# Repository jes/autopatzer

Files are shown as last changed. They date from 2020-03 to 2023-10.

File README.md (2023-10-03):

# autopatzer

An automatic chess board, supporting online play with people all over the world via the [Lichess Boards API](https://lichess.org/blog/XlRW5REAAB8AUJJ-/welcome-lichess-boards).

This repo contains FreeCAD files for the mechanical design, KiCad files for PCB design, Arduino code to run on
the microcontroller, Perl code for the library/program that interfaces with the controller, and JavaScript code for the
user interface and Lichess interface.

You can [watch a video of the board](https://www.youtube.com/watch?v=8ScFtkWvHW8) if you want.

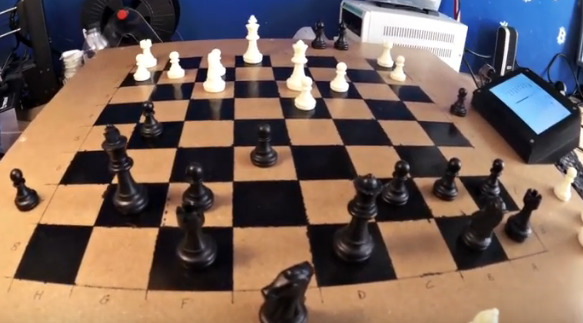
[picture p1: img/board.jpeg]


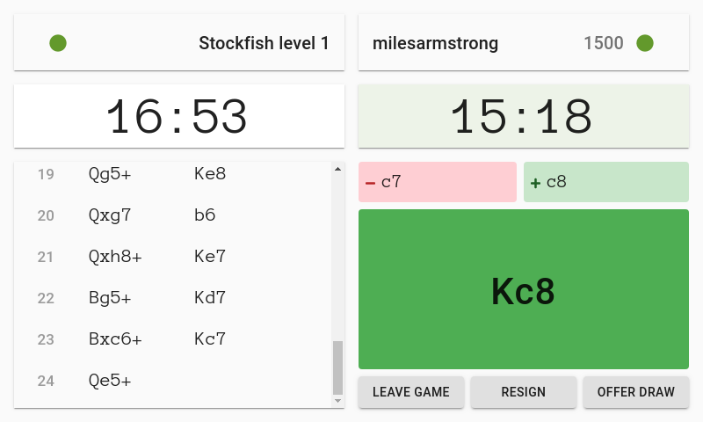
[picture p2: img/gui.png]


## Build one yourself

I thoroughly encourage you to build an Autopatzer board. You'll need:

 - 3d printer
 - soldering skills
 - general DIY skills
 - and it would probably help to have prior experience with Arduino and Raspberry Pi

There aren't currently a decent set of instructions, so if you want to build one let's try and write some
instructions as you go so that it might be easier for whoever comes next!

There are some notes about how you might want to change the design in my blog post: https://incoherency.co.uk/blog/stories/autopatzer.html

## Architecture

There is a NEMA17 stepper motor for each of the X and Y axis, from an old 3d printer. The stepper motors are controlled by A4988 stepper
motor drivers, which are controlled using the step/direction pins, driven by the AccelStepper Arduino library. The electromagnet is switched
on and off with a MOSFET. The pieces are detected with an analogue hall effect sensor under each square. These 64 analogue signals are reduced
to 8 signals with 8x CD4051 8-to-1 analogue multiplexers. All of the code for this runs on a Teensy 3.2 microcontroller, and the rest is
adequately explained by this diagram:

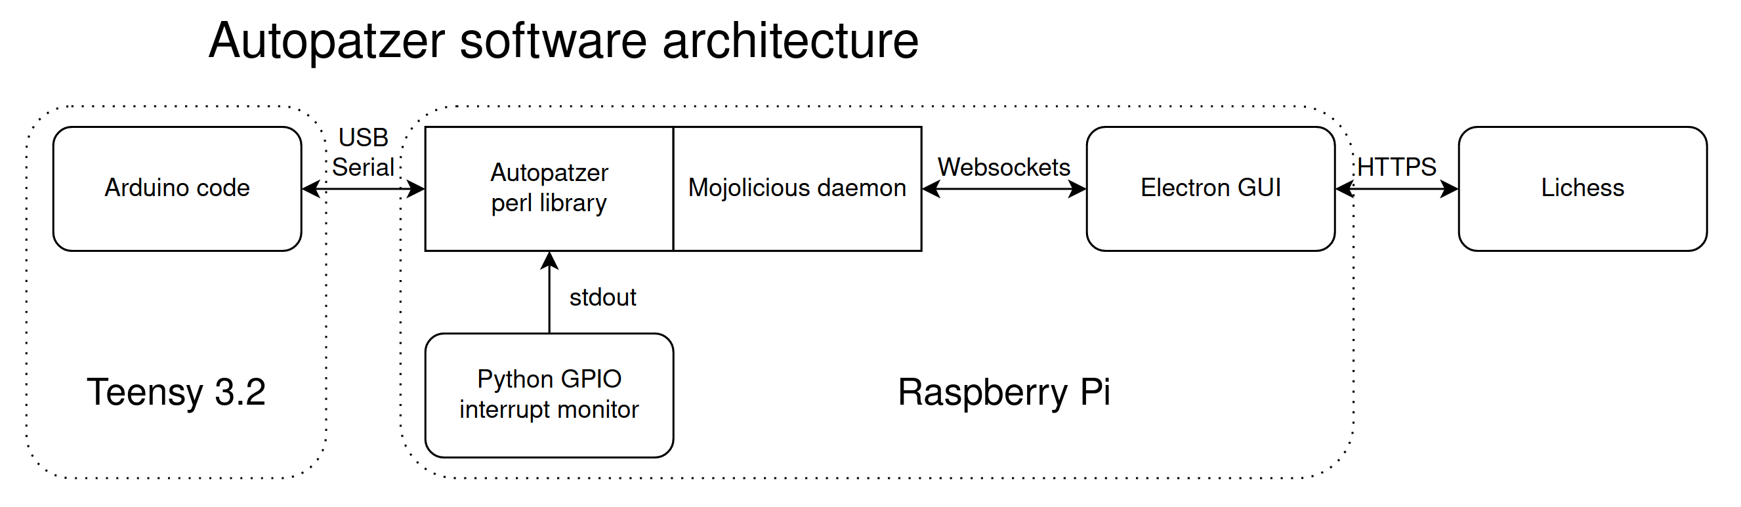
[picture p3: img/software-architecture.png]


## Contact

The Electron app providing the user interface is by Miles Armstrong: miles@milesarmstrong.co.uk

The rest is by James Stanley: james@incoherency.co.uk

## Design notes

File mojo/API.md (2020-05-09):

# Autopatzer websocket API

Connect with websocket to ws://localhost:3001/ws

All messages are asynchronous.

Game state is stored in the mojo daemon, we probably don't need the JS part
to store game state. If we reach a point where we want JS to store game state
we should consider whether it might just be easier to move those parts into
mojolicious and add some websocket message types.

Notably missing from this specification so far is any way for the JS part (and
therefore the user) to request some information about what the current board position
should be, so if they accidentally kick all the pieces over they better either remember
what squares they go on, or manually replay the entire game by following the
moves which should be displayed on the interface (like "1. e4 e5 2. Nf3 Nf6" etc.).

All messages are JSON hashes (dictionaries? objects?). Messages which are not a hash (e.g.
arrays or scalars) are illegal.
Message types are identified by the "op" field, which is present in all messages.
Upon receipt of a message we need to switch on "op" and then handle it accordingly.
Messages which do not contain "op" are illegal.

Implicit in this specification is that Mojolicious and the JS app are both synchronised
with regards to where they are in the game state (i.e. that the board is in the starting
position, and JS app joins lichess at the start of the game). If this condition is likely
to be violated then we probably have more to do (e.g. just tell the user "please set up
the pieces like this" with a diagram of the board, and then send FEN of the position
to Mojo so that Mojo knows what the position is).

## Messages from web page to mojolicious

### Play move

    {"op":"play","move":"Ne5"}

When lichess reports that the other player has made a move, immediately send it onwards
to Mojolicious so that the board state can be updated & the move can be made on the physical
board using the stepper motors.

When the player has made a move (which he confirms by hitting the clock button, see below),
then also use this function to send the move to Mojo.

Mojo won't know or care whether the local player is black or white, it's up to the JS app
to just tell Mojo which moves to commit to, for both players.

### Reset internal game state

    {"op":"reset","moves":["d4","d5","Bf4","Nf6"}

This tells Mojolicious app to reset its game state to the start of the game. It won't automatically
reset the physical board (and it's not possible e.g. for captured pieces to be automatically
returned to the starting position), so we probably also want a message telling the user to reset
the board. Ideally the JS app would ask for the board to be reset *before* seeking another game,
instead of after, otherwise the first move of the game will time out while the user is busy
resetting the pieces.

If "moves" is present, then Mojolicious app will play through those moves after resetting to the
start state.

### Wiggle the motors to make a noise to alert the user

    {"op":"wiggle"}

This will cause the motors to be moved back and forth briefly, to make a noise, to alert the user.
It should (only?) be sent when we've received gameFull and the user is playing white.

### Ping

    {"op":"ping"}

Just used to keep connection alive. Ignored by the server. The client does not need to send these,
it should be enough for the server to do all the keeping alive.

## Messages from mojolicious to web page

### Report changes made on board

    {"op":"board","move":"","lost":["f3"],"gained":[]}
    {"op":"board","move":"Ne5","lost":["f3"],"gained":["e5"]}

In response to this the JS app should display some box showing the detected move. If
no detected move is given, it should instead show which squares changed (e.g. write in
red "- f3" and write in green "+ e5"). There can be arbitrarily many squares
changed, because the user can just pick the pieces up and move them around, but unless
there is a legal move, there's nothing to do apart from tell them which squares have
changed. If there *is* a legal move, then the JS app should store it so that if the
user then hits the clock button, the JS app can tell the Mojo app to commit to the
move. Also, if the move is a pawn promotion, the JS app should default to promoting
to Queen, but should have some way for the user to select between Knight/Bishop/Rook/Queen.

If it is not currently the user's turn (i.e. we're waiting on the remote lichess player)
but the board reports the board position changed anyway, then probably just show the same
stuff anyway so that the user has a chance to put the pieces back.

### Report clock button hit

    {"op":"button"}

This means the button next to the screen has been pressed, which means the user wants to
commit to a move. If it is the user's turn, then now is the time to send an "op":"play" message with
the latest reported move. If it is not the user's turn then probably either do nothing or
show "Not your turn". Do nothing is probably fine and easier.

### Ping

    {"op":"ping"}

Just used to keep connection alive. Ignored by the client. The server needs to send these
periodically to ensure the connection does not timeout in the event of a long think with
nothing happening.

### Error

    {"op":"error","error":"Illegal move: Ne5"}

If the JS app is working correctly I can't think of anything that could trigger an
error message, so probably if it receives one it should pop it up on the screen so
we know what needs debugging.

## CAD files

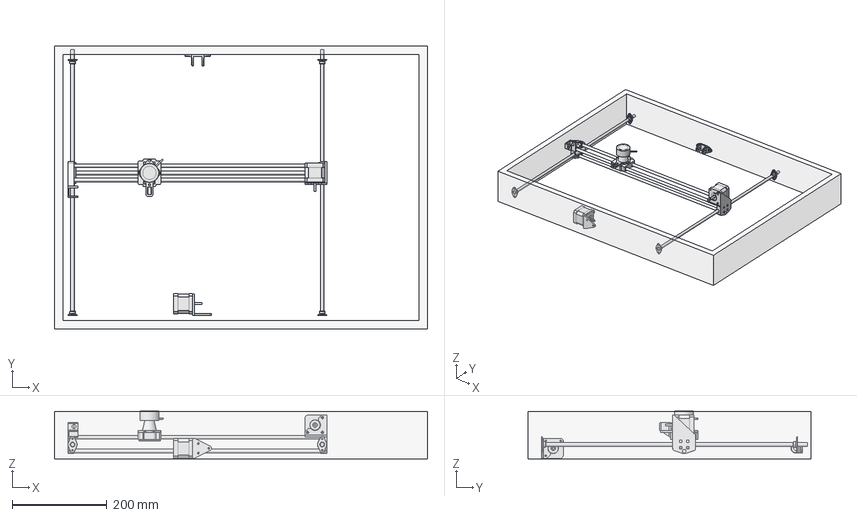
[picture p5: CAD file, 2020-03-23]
freecad/assembly.FCStd
786.0 x 596.0 x 100.1 mm
woodenframe_001
railbracket_001
railbracket_002
railbracket_003
railbracket_004
linearbearing_001
linearbearing_002
xbracket-idler_001
linearrod_003
linearrod_004
xbracket-stepper_001
linearbearing_003
linearbearing_004
carriage_001
electromagnet_001
NEMA-17_Stepper_Motor_40mm_001
ybracket-stepper_001
NEMA-17_Stepper_Motor_40mm_002
ybracket-idler_001
linearrod_005
ylinearrod_001
ylinearrod_002

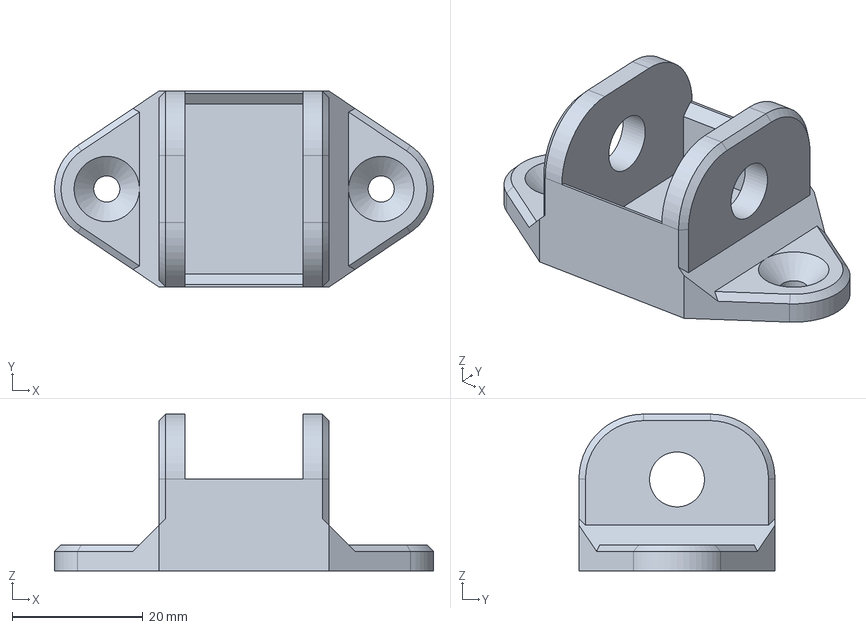
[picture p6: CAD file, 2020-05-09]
freecad/ybracket-idler.FCStd
58.0 x 30.0 x 24.0 mm

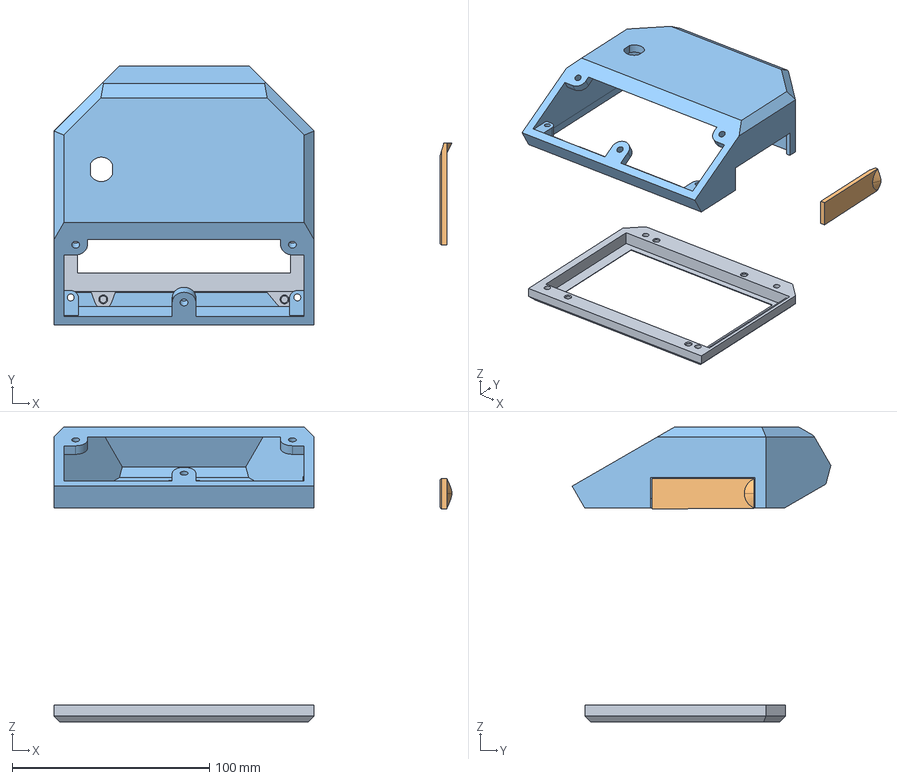
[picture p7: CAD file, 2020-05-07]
freecad/picase.FCStd
202.0 x 131.3 x 149.7 mm
pifront
iocover
maincase

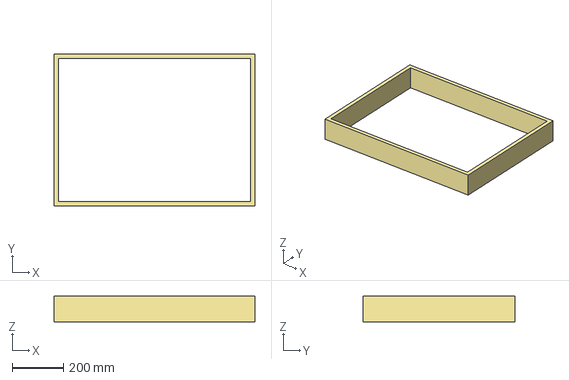
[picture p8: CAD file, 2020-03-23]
freecad/woodenframe.FCStd
786.0 x 596.0 x 100.0 mm

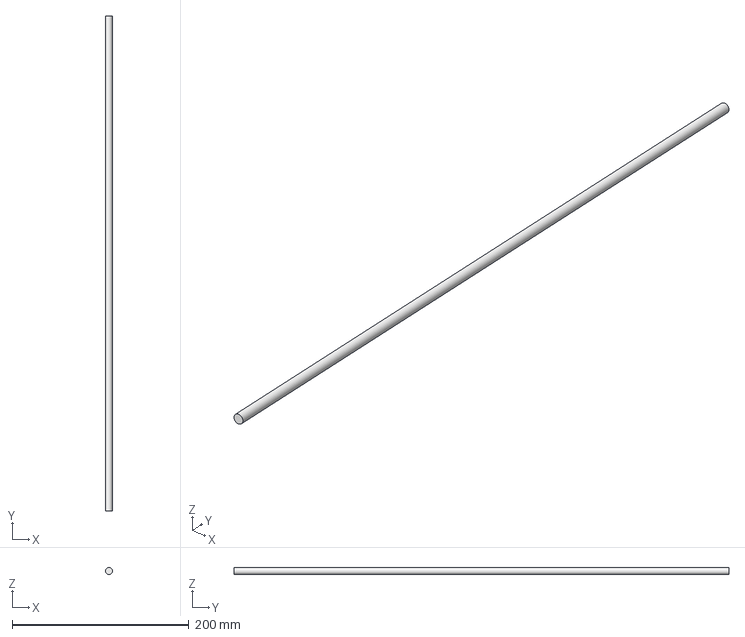
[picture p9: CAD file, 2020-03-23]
freecad/ylinearrod.FCStd
7.99 x 560.0 x 8.00 mm

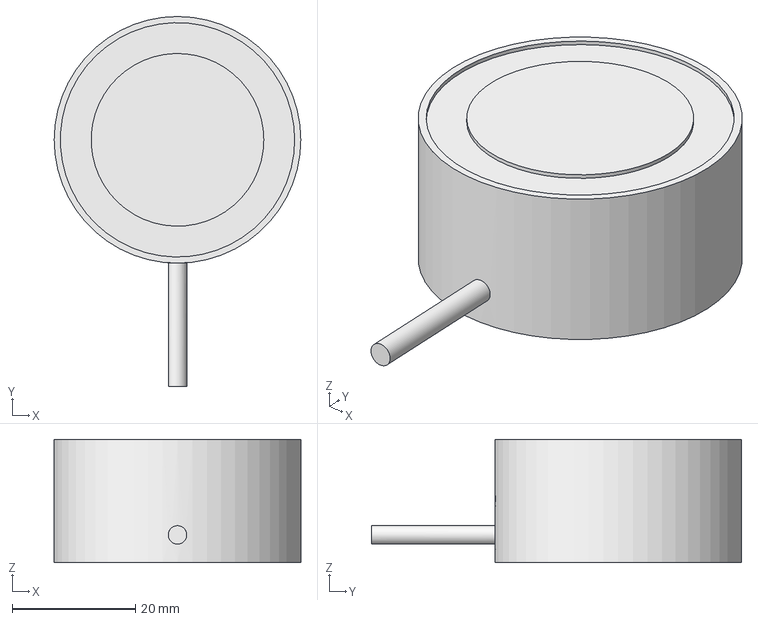
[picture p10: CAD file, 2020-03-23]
freecad/electromagnet.FCStd
40.0 x 60.0 x 20.0 mm

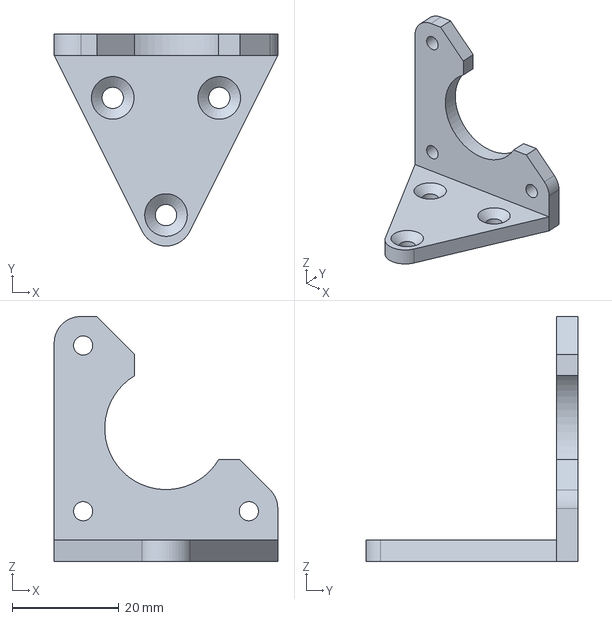
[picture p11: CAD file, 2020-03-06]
freecad/ybracket-stepper.FCStd
42.0 x 39.8 x 46.0 mm

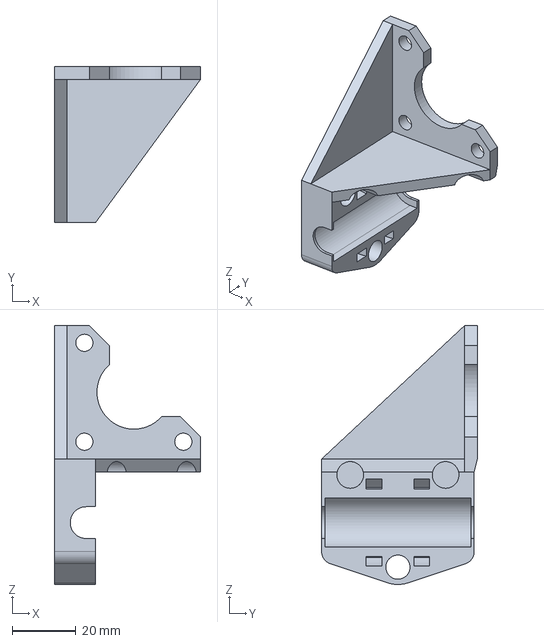
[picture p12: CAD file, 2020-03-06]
freecad/xbracket-stepper.FCStd
46.0 x 49.0 x 81.5 mm

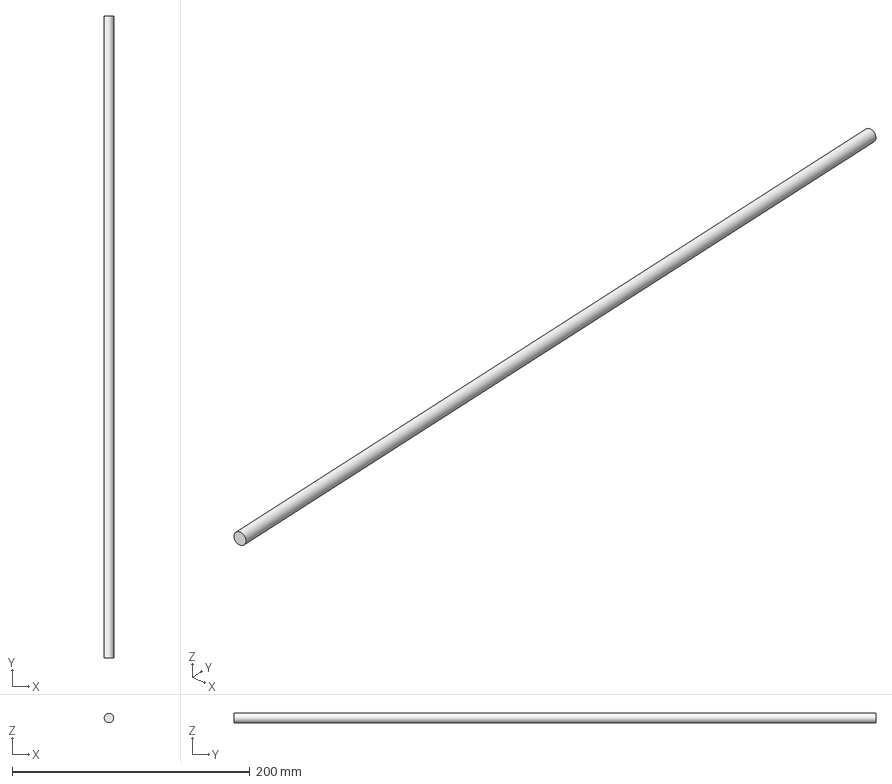
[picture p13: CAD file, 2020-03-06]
freecad/linearrod.FCStd
7.99 x 540.0 x 8.00 mm

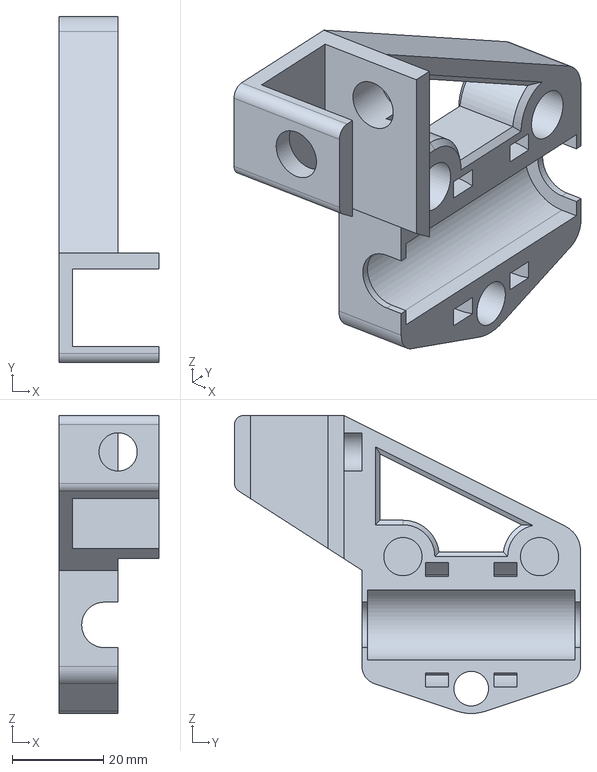
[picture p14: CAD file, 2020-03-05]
freecad/xbracket-idler.FCStd
22.0 x 76.0 x 65.5 mm

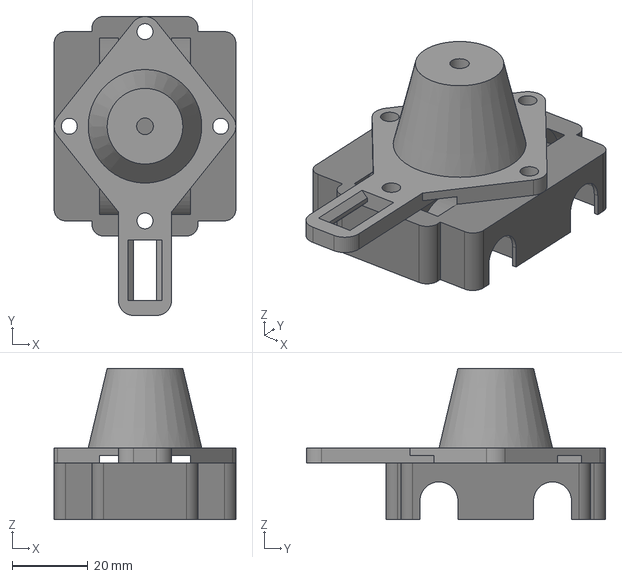
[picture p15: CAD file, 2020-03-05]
freecad/carriage.FCStd
48.0 x 79.0 x 40.0 mm

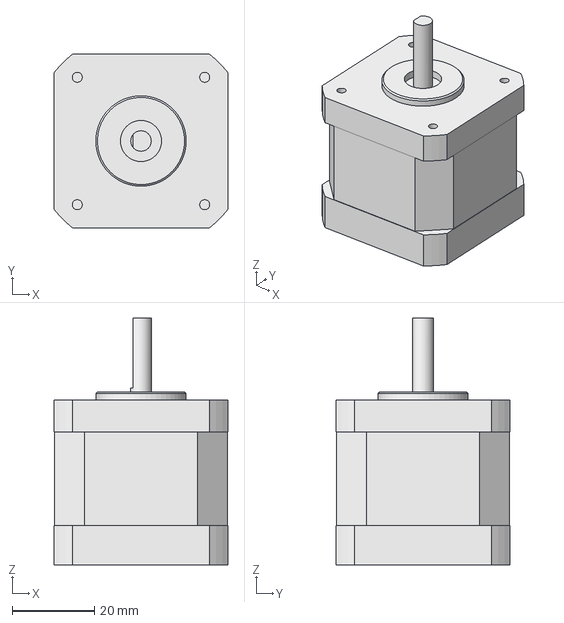
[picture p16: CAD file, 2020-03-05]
freecad/NEMA-17_Stepper_Motor_40mm.fcstd
42.3 x 42.3 x 60.1 mm

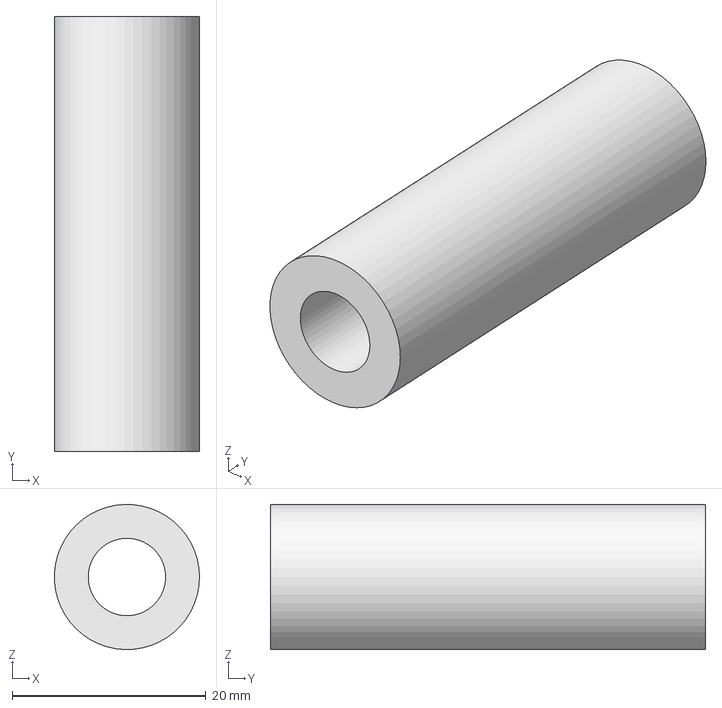
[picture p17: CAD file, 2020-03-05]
freecad/linearbearing.FCStd
15.0 x 45.0 x 15.0 mm

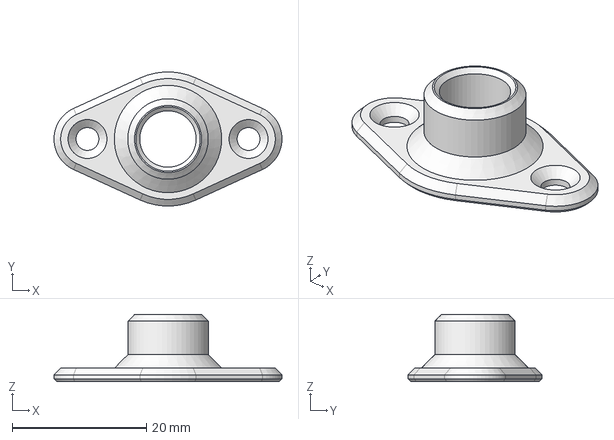
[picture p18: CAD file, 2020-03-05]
freecad/railbracket.FCStd
34.0 x 20.0 x 10.0 mm

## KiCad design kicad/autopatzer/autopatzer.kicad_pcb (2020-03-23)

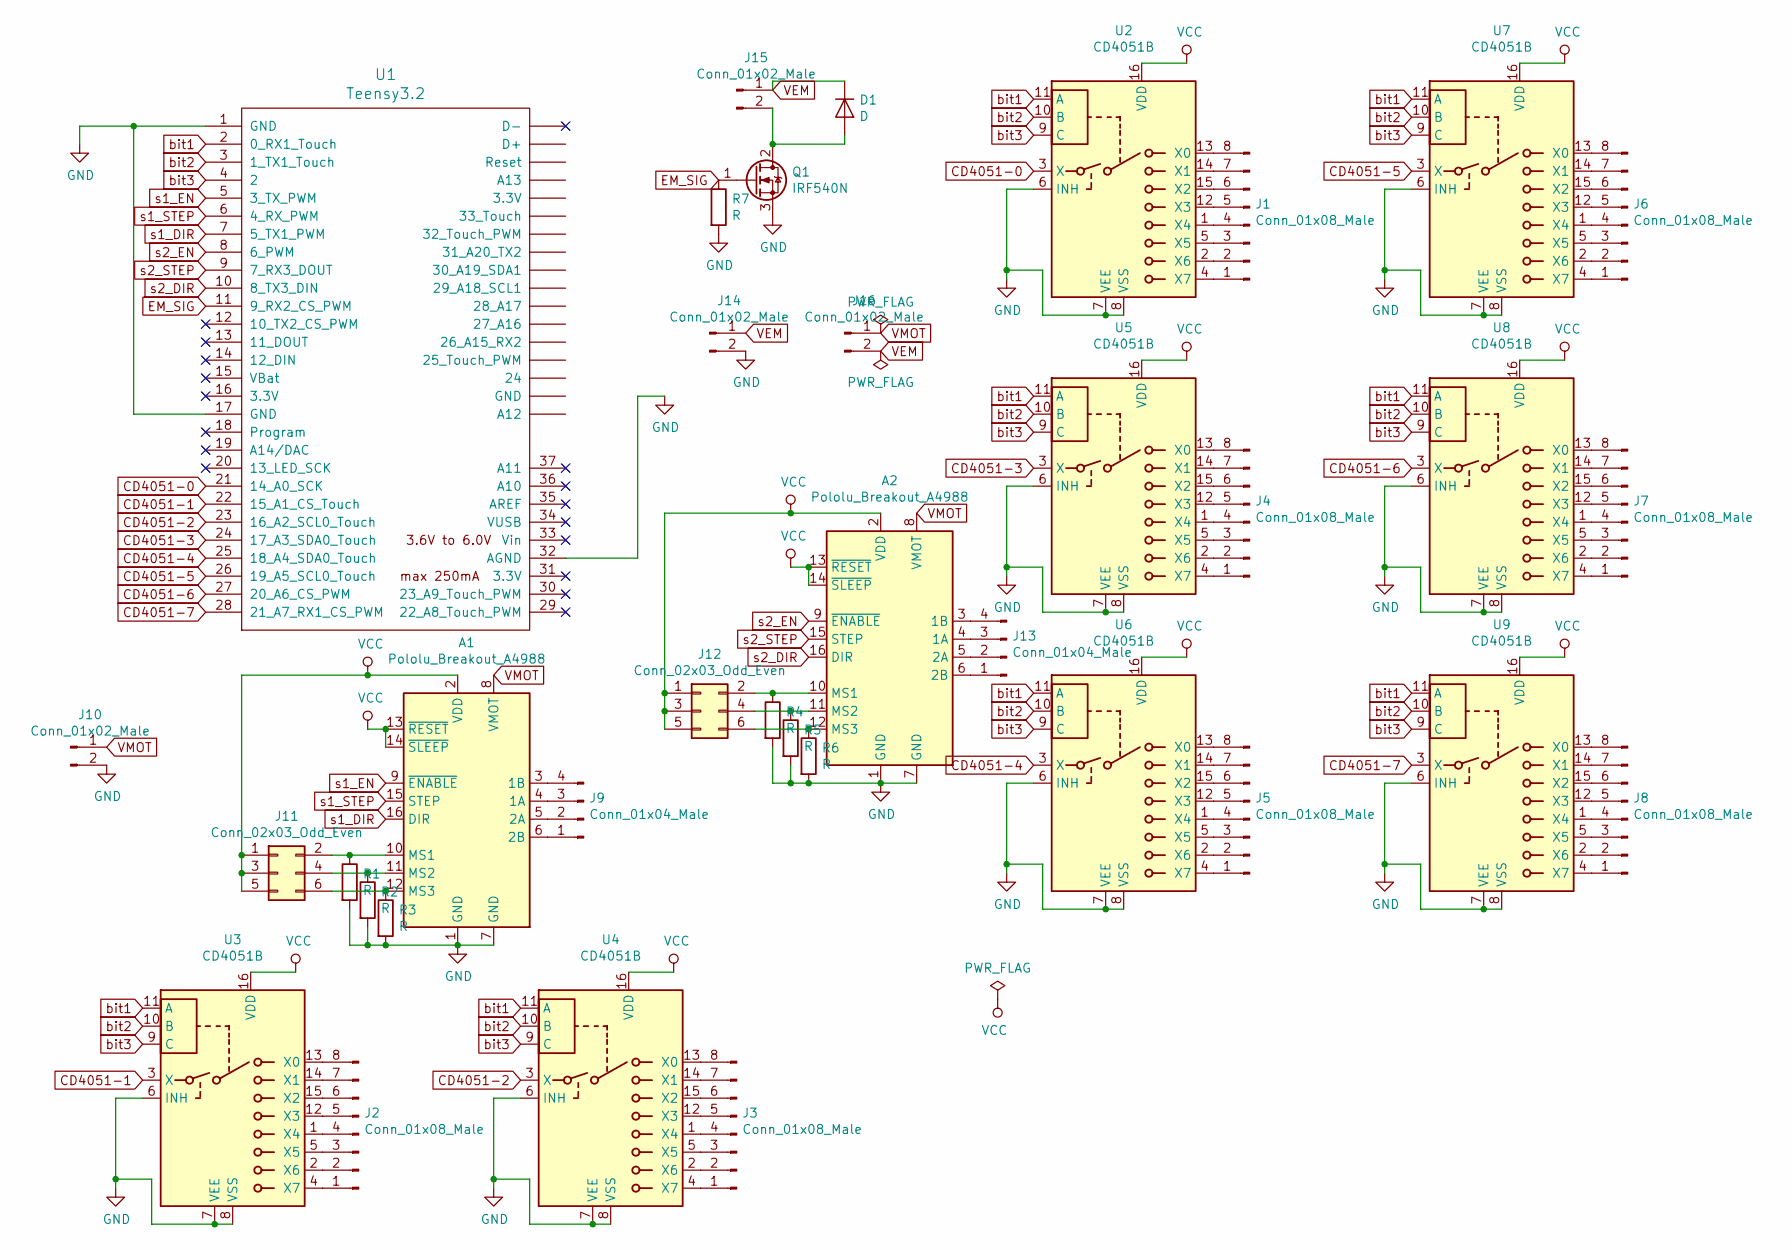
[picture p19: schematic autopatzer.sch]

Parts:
A1, A2: Pololu_Breakout_A4988; Pololu_Breakout-16_15.2x20.3mm
D1: D; D_5W_P12.70mm_Horizontal
J1, J2, J3, J4, J5, J6, J7, J8: Conn_01x08_Male; PinHeader_1x08_P2.54mm_Vertical
J9, J13: Conn_01x04_Male; PinHeader_1x04_P2.54mm_Vertical
J10, J14, J15, J16: Conn_01x02_Male; PinHeader_1x02_P2.54mm_Vertical
J11, J12: Conn_02x03_Odd_Even; PinHeader_2x03_P2.54mm_Vertical
Q1: IRF540N; TO-220-3_Vertical
R1, R2, R3, R4, R5, R6, R7: R; R_Axial_DIN0411_L9.9mm_D3.6mm_P12.70mm_Horizontal
U1: Teensy3.2; Teensy30_31_32_LC
U2, U3, U4, U5, U6, U7, U8, U9: CD4051B; DIP-16_W7.62mm

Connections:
CD4051-0: U1.21 (14_A0_SCK), U2.3 (X)
CD4051-1: U1.22 (15_A1_CS_Touch), U3.3 (X)
CD4051-2: U1.23 (16_A2_SCL0_Touch), U4.3 (X)
CD4051-3: U1.24 (17_A3_SDA0_Touch), U5.3 (X)
CD4051-4: U1.25 (18_A4_SDA0_Touch), U6.3 (X)
CD4051-5: U1.26 (19_A5_SCL0_Touch), U7.3 (X)
CD4051-6: U1.27 (20_A6_CS_PWM), U8.3 (X)
CD4051-7: U1.28 (21_A7_RX1_CS_PWM), U9.3 (X)
EM_SIG: Q1.1 (G), R7.1, U1.11 (9_RX2_CS_PWM)
GND: A1.1 (GND), A1.7 (GND), A2.1 (GND), A2.7 (GND), J10.2, J14.2, Q1.3 (S), R1.2, R2.2, R3.2, R4.2, R5.2, R6.2, R7.2, U1.1 (GND), U1.17 (GND), U1.32 (AGND), U2.6 (INH), U2.7 (VEE), U2.8 (VSS), U3.6 (INH), U3.7 (VEE), U3.8 (VSS), U4.6 (INH), U4.7 (VEE), U4.8 (VSS), U5.6 (INH), U5.7 (VEE), U5.8 (VSS), U6.6 (INH), U6.7 (VEE), U6.8 (VSS), U7.6 (INH), U7.7 (VEE), U7.8 (VSS), U8.6 (INH), U8.7 (VEE), U8.8 (VSS), U9.6 (INH), U9.7 (VEE), U9.8 (VSS)
unnamed: A1.3 (1B), J9.4
unnamed: A1.4 (1A), J9.3
unnamed: A1.5 (2A), J9.2
unnamed: A1.6 (2B), J9.1
unnamed: A1.10 (MS1), J11.2, R1.1
unnamed: A1.11 (MS2), J11.4, R2.1
unnamed: A1.12 (MS3), J11.6, R3.1
unnamed: A2.3 (1B), J13.4
unnamed: A2.4 (1A), J13.3
unnamed: A2.5 (2A), J13.2
unnamed: A2.6 (2B), J13.1
unnamed: A2.10 (MS1), J12.2, R4.1
unnamed: A2.11 (MS2), J12.4, R5.1
unnamed: A2.12 (MS3), J12.6, R6.1
unnamed: D1.2 (A), J15.2, Q1.2 (D)
unnamed: J1.1, U2.4 (X7)
unnamed: J1.2, U2.2 (X6)
unnamed: J1.3, U2.5 (X5)
unnamed: J1.4, U2.1 (X4)
unnamed: J1.5, U2.12 (X3)
unnamed: J1.6, U2.15 (X2)
unnamed: J1.7, U2.14 (X1)
unnamed: J1.8, U2.13 (X0)
unnamed: J2.1, U3.4 (X7)
unnamed: J2.2, U3.2 (X6)
unnamed: J2.3, U3.5 (X5)
unnamed: J2.4, U3.1 (X4)
unnamed: J2.5, U3.12 (X3)
unnamed: J2.6, U3.15 (X2)
unnamed: J2.7, U3.14 (X1)
unnamed: J2.8, U3.13 (X0)
unnamed: J3.1, U4.4 (X7)
unnamed: J3.2, U4.2 (X6)
unnamed: J3.3, U4.5 (X5)
unnamed: J3.4, U4.1 (X4)
unnamed: J3.5, U4.12 (X3)
unnamed: J3.6, U4.15 (X2)
unnamed: J3.7, U4.14 (X1)
unnamed: J3.8, U4.13 (X0)
unnamed: J4.1, U5.4 (X7)
unnamed: J4.2, U5.2 (X6)
unnamed: J4.3, U5.5 (X5)
unnamed: J4.4, U5.1 (X4)
unnamed: J4.5, U5.12 (X3)
unnamed: J4.6, U5.15 (X2)
unnamed: J4.7, U5.14 (X1)
unnamed: J4.8, U5.13 (X0)
unnamed: J5.1, U6.4 (X7)
unnamed: J5.2, U6.2 (X6)
unnamed: J5.3, U6.5 (X5)
unnamed: J5.4, U6.1 (X4)
unnamed: J5.5, U6.12 (X3)
unnamed: J5.6, U6.15 (X2)
unnamed: J5.7, U6.14 (X1)
unnamed: J5.8, U6.13 (X0)
unnamed: J6.1, U7.4 (X7)
unnamed: J6.2, U7.2 (X6)
unnamed: J6.3, U7.5 (X5)
unnamed: J6.4, U7.1 (X4)
unnamed: J6.5, U7.12 (X3)
unnamed: J6.6, U7.15 (X2)
unnamed: J6.7, U7.14 (X1)
unnamed: J6.8, U7.13 (X0)
unnamed: J7.1, U8.4 (X7)
unnamed: J7.2, U8.2 (X6)
unnamed: J7.3, U8.5 (X5)
unnamed: J7.4, U8.1 (X4)
unnamed: J7.5, U8.12 (X3)
unnamed: J7.6, U8.15 (X2)
unnamed: J7.7, U8.14 (X1)
unnamed: J7.8, U8.13 (X0)
unnamed: J8.1, U9.4 (X7)
unnamed: J8.2, U9.2 (X6)
unnamed: J8.3, U9.5 (X5)
unnamed: J8.4, U9.1 (X4)
unnamed: J8.5, U9.12 (X3)
unnamed: J8.6, U9.15 (X2)
unnamed: J8.7, U9.14 (X1)
unnamed: J8.8, U9.13 (X0)
VCC: A1.2 (VDD), A1.13 (~RESET), A1.14 (~SLEEP), A2.2 (VDD), A2.13 (~RESET), A2.14 (~SLEEP), J11.1, J11.3, J11.5, J12.1, J12.3, J12.5, U2.16 (VDD), U3.16 (VDD), U4.16 (VDD), U5.16 (VDD), U6.16 (VDD), U7.16 (VDD), U8.16 (VDD), U9.16 (VDD)
VEM: D1.1 (K), J14.1, J15.1, J16.2
VMOT: A1.8 (VMOT), A2.8 (VMOT), J10.1, J16.1
bit1: U1.2 (0_RX1_Touch), U2.11 (A), U3.11 (A), U4.11 (A), U5.11 (A), U6.11 (A), U7.11 (A), U8.11 (A), U9.11 (A)
bit2: U1.3 (1_TX1_Touch), U2.10 (B), U3.10 (B), U4.10 (B), U5.10 (B), U6.10 (B), U7.10 (B), U8.10 (B), U9.10 (B)
bit3: U1.4 (2), U2.9 (C), U3.9 (C), U4.9 (C), U5.9 (C), U6.9 (C), U7.9 (C), U8.9 (C), U9.9 (C)
s1_DIR: A1.16 (DIR), U1.7 (5_TX1_PWM)
s1_EN: A1.9 (~ENABLE), U1.5 (3_TX_PWM)
s1_STEP: A1.15 (STEP), U1.6 (4_RX_PWM)
s2_DIR: A2.16 (DIR), U1.10 (8_TX3_DIN)
s2_EN: A2.9 (~ENABLE), U1.8 (6_PWM)
s2_STEP: A2.15 (STEP), U1.9 (7_RX3_DOUT)

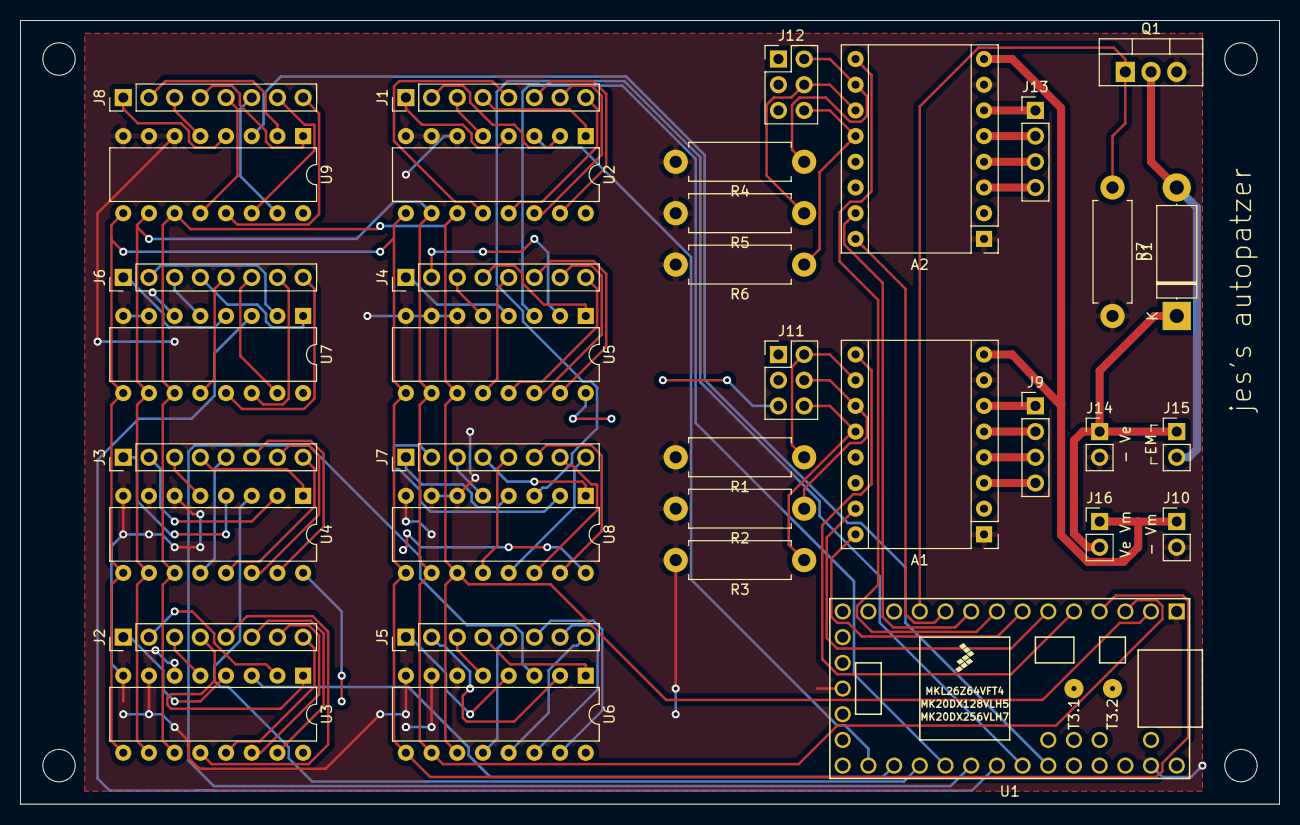
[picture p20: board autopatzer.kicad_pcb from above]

Board: 2 copper layers, 124.5 x 77.5 mm, 36 parts (0 on the bottom side), 101 nets.

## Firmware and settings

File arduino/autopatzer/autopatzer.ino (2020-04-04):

/* Main control code for autopatzer
 *  
 *  James Stanley 2020
 */

#define BUFSZ 128

extern bool realSquareOccupied[64];
extern bool magnetState;
extern const int squareSize;

unsigned long magnetActivated;
unsigned long lastMovement;

void setup() {
  Serial.begin(9600); // XXX: faster?

  // stepper motors
  initSteppers(3, 4, 5, 6, 7, 8);
  homeSteppers();

  // hall sensors
  initHallSensors(0, 1, 2);

  // electromagnet
  initMagnet();
  
  Serial.println("autopatzer ready");
}

// x = rank, y = file
void movePiece(int startx, int starty, int endx, int endy) {
  targetSteppers(startx*480, starty*480, 0);
  while (!finishedSteppers()) updateSteppers();
  grabMagnet();
  targetSteppers(endx*480, endy*480, 1);
  while (!finishedSteppers()) updateSteppers();
  releaseMagnet();
}


void loop() {
  updateHallSensors();
  updateSteppers();
  updateMagnet();
  updateSerial();

  if (!finishedSteppers())
    lastMovement = millis();
}

void updateSerial() {
  static char buf[BUFSZ];
  static int p;
  
  while (Serial.available() > 0) {
    char c = Serial.read();
    if (c == '\r' || c== '\n' || p == BUFSZ-1) {
      buf[p++] = 0;
      serialCommand(buf);
      p = 0;
    } else {
      buf[p++] = c;
    }
  }
}

void serialCommand(char *buf) {
  char **params = split(buf);

  if (strcmp(params[0], "help") == 0) {
    Serial.print(
      "autopatzer commands:\r\n"
      "   help           - show help\r\n"
      "   goto X Y       - move motors to (X,Y)\r\n"
      "   wait           - wait for motors to stop\r\n"
      "   grab           - switch electromagnet on\r\n"
      "   release        - switch electromagnet off\r\n"
      "   scan           - scan hall effect sensors\r\n"
      "   home           - re-home the motors\r\n"
    );
      
  } else if (strcmp(params[0], "goto") == 0) {
    if (!params[1] || !params[2]) {
      Serial.println("error: usage: goto X Y");
      return;
    }
  
    float x = atof(params[1]);
    float y = atof(params[2]);
    if (x < 0 || x > 9) {
      Serial.println("error: X must be from 0 to 9");
      return;
    }
    if (y < 0 || y > 9) {
      Serial.println("error: Y must be from 0 to 9");
      return;
    }

    x += 0.1;

    targetSteppers(x * squareSize, y * squareSize, magnetState);
    
  } else if (strcmp(params[0], "wait") == 0) {
    if (!finishedSteppers()) {
      runSteppers();
      lastMovement = millis();
    }
    Serial.println("waited");
    
  } else if (strcmp(params[0], "grab") == 0) {
    grabMagnet();
    
  } else if (strcmp(params[0], "release") == 0) {
    releaseMagnet();
    
  } else if (strcmp(params[0], "scan") == 0) {
    Serial.print("occupied:");
    for (int i = 0; i < 64; i++) {
      if (realSquareOccupied[i]) {
        Serial.print(" ");
        Serial.print(square2Name(i));
      }
    }
    Serial.println("");

    //analogScanHallSensors();
    
  } else if (strcmp(params[0], "home") == 0) {
    homeSteppers();
    
  }
}

// replace each space in buf with a \0, and return a (static!) nul-terminated array of pointers to the string parts
char **split(char *buf) {
  static char *parts[16];
  int n = 0;
  
  char *p = buf;
  while (*p && n < 15) {
    parts[n++] = p;
    while (*p && *p != ' ')
      p++;
    if (*p == ' ')
      *(p++) = 0;
  }
  parts[n++] = 0;
  
  return parts;
}

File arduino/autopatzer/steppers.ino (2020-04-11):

/* Stepper motor control code for autopatzer
 *  
 *  James Stanley 2020
 */

#include <AccelStepper.h>

AccelStepper stepper[2];

extern bool realSquareOccupied[64];

const int squareSize = 480; // steps per square

// configure max. velocity and acceleration while grabbed and not grabbed
const int maxvel[2] = {4000 /*released*/, 3000 /*grabbed*/}; // steps per sec
const int maxacc[2] = {20000 /*released*/, 6000 /*grabbed*/}; // steps per sec^2

const int home1 = 4330;
const int home2 = 4360;
const int extrahome = 200;

const bool invert1 = true;
const bool invert2 = false;

void initSteppers(int en1, int step1, int dir1, int en2, int step2, int dir2) {
  AccelStepper s0(AccelStepper::DRIVER, step1, dir1);
  pinMode(en1, OUTPUT);
  digitalWrite(en1, LOW);
  AccelStepper s1(AccelStepper::DRIVER, step2, dir2);
  pinMode(en2, OUTPUT);
  digitalWrite(en2, LOW);
  
  stepper[0] = s0;
  stepper[1] = s1;
}

void targetSteppers(int x, int y, int magnetState) {
  if (invert1)
    x = -x;
  if (invert2)
    y = -y;

  stepper[0].moveTo(x);
  stepper[0].setMaxSpeed(maxvel[magnetState]);
  stepper[0].setAcceleration(maxacc[magnetState]);
  
  stepper[1].moveTo(y);
  stepper[1].setMaxSpeed(maxvel[magnetState]);
  stepper[1].setAcceleration(maxacc[magnetState]);
}

void updateSteppers() {
  stepper[0].run();
  stepper[1].run();
}

void runSteppers() {
  while (!finishedSteppers())
    updateSteppers();
}

bool finishedSteppers() {
  return stepper[0].distanceToGo() == 0 && stepper[1].distanceToGo() == 0;
}

bool magnetHomeSteppers() {
  bool squareWasOccupied[64];

  delay(250);

  releaseMagnet();
  waitHallSensors(100);
  for (int i = 0; i < 64; i++)
    squareWasOccupied[i] = realSquareOccupied[i];
  grabMagnet();
  waitHallSensors(100);

  int homingSquare = -1;

  for (int i = 0; i < 64; i++) {
    if (realSquareOccupied[i] && !squareWasOccupied[i]) {
        homingSquare = i;
        break;
    }
  }

  if (homingSquare == -1) {
    releaseMagnet();
    return false;
  }

  // now move around to detect the centre point of where we're detected
  binarySearchOnSquare(0, homingSquare);
  binarySearchOnSquare(1, homingSquare);

  releaseMagnet();
  waitHallSensors(100);

  stepper[0].setCurrentPosition(squareSize * (homingSquare%8 + 1) * (invert1 ? -1 : 1));
  stepper[1].setCurrentPosition(squareSize * (homingSquare/8 + 1) * (invert2 ? -1 : 1));

  // TODO: validate by moving to an unoccupied square and switching the magnet on and off?

  return true;
}

void binarySearchOnSquare(int motor, int sqr) {
  const int threshold = 20;
  int minLimit = 0;
  int maxLimit = 0;
  int minpos, maxpos;

  stepper[motor].setCurrentPosition(0);
  stepper[0].setMaxSpeed(maxvel[0]);
  stepper[0].setAcceleration(maxacc[0]);
  
  minpos = -squareSize/2;
  maxpos = 0;
  // find the smallest position from minpos to maxpos that is occupied
  while (minpos+threshold < maxpos) {
    int midpos = (minpos+maxpos)/2;
    stepper[motor].moveTo(midpos);
    runSteppers();
    waitHallSensors(100);
    if (realSquareOccupied[sqr]) {
      maxpos = midpos;
    } else {
      minpos = midpos+1;
    }
  }
  minLimit = minpos;
  
  minpos = 0;
  maxpos = squareSize/2;
  // find the largest position from minpos to maxpos that is occupied
  while (minpos+threshold < maxpos) {
    int midpos = (minpos+maxpos)/2;
    stepper[motor].moveTo(midpos);
    runSteppers();
    waitHallSensors(100);
    if (!realSquareOccupied[sqr]) {
      maxpos = midpos-1;
    } else {
      minpos = midpos;
    }
  }
  maxLimit = minpos;

  // finally, move to the centre point of the min and max limit
  stepper[motor].moveTo((minLimit + maxLimit) / 2);
  runSteppers();
}

void homeSteppers() {
  // first try to home it using the electromagnet
  //if (magnetHomeSteppers())
  //  return;
    
  stepper[0].setCurrentPosition(0);
  stepper[1].setCurrentPosition(0);

  // "crash homing": just drive the maximum distance until we know we've crashed into the end
  targetSteppers(home1+extrahome, home2+extrahome, 0);
  runSteppers();

  // now drive back to 0,0 to home
  stepper[0].setCurrentPosition(home1 * (invert1 ? -1 : 1));
  stepper[1].setCurrentPosition(home2 * (invert2 ? -1 : 1));
  targetSteppers(0, 0, 0);
  runSteppers();
}

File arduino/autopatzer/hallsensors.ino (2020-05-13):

/* Hall sensor code for autopatzer
 *  
 * James Stanley 2020
 */

const int pieceSettleMs = 50; // don't report a square changed until it has settled for N ms

bool squareOccupied[64];
bool realSquareOccupied[64];
unsigned long lastChange[64];

// map sensor locations to actual squares (0=a1, 7=a8, 8=b1, 56=h1, 63=h8)
int squareMap[64] = {
  36, 29, 18, 43, 59, 12, 49,  4,
  32, 31, 21, 45, 61, 15, 52,  0,
  34, 26, 20, 42, 56,  9, 54,  2,
  38, 24, 16, 44, 60, 11, 50,  5,
  35, 27, 17, 40, 58, 10, 53,  7,
  37, 30, 19, 47, 63, 13, 55,  6,
  39, 28, 23, 46, 62,  8, 51,  3,
  33, 25, 22, 41, 57, 14, 48,  1,
};

// we set a different threshold for each square
int analogThreshold[64] = {
//  1    2    3    4    5    6    7    8
  715, 745, 695, 705, 690, 650, 690, 730, // a
  715, 680, 715, 735, 675, 725, 675, 730, // b
  740, 705, 695, 655, 680, 710, 730, 715, // c
  720, 690, 740, 720, 705, 690, 640, 715, // d
  710, 755, 670, 695, 640, 710, 715, 750, // e
  700, 745, 675, 705, 725, 690, 715, 705, // f
  660, 700, 630, 645, 710, 725, 720, 725, // g
  725, 675, 690, 680, 720, 675, 680, 710, // h
};

int bit1pin, bit2pin, bit3pin;

void initHallSensors(int bit1, int bit2, int bit3) {
  bit1pin = bit1;
  bit2pin = bit2;
  bit3pin = bit3;
  pinMode(bit1, OUTPUT);
  pinMode(bit2, OUTPUT);
  pinMode(bit3, OUTPUT);

  scanHallSensors();
  for (int i = 0; i < 64; i++)
    realSquareOccupied[i] = squareOccupied[i];
}

void waitHallSensors(int ms) {
  unsigned long start = millis();

  while (millis() < start+ms) {
    updateHallSensors();
  }
}

void updateHallSensors() {
  scanHallSensors();
  for (int i = 0; i < 64; i++) {
    if (millis() - lastChange[i] > pieceSettleMs && squareOccupied[i] != realSquareOccupied[i]) {
      realSquareOccupied[i] = squareOccupied[i];
      if (realSquareOccupied[i] ) {
        Serial.print("piecedown "); Serial.println(square2Name(i));
      } else {
        Serial.print("pieceup "); Serial.println(square2Name(i));
      }
    }
  }
}

void scanHallSensors() {
  for (int i = 0; i < 8; i++) {
    digitalWrite(bit1pin, i&1);
    digitalWrite(bit2pin, i&2);
    digitalWrite(bit3pin, i&4);
    // XXX: do we need to wait between writing to the bit pins and reading from the analogue pins?
    for (int j = 0; j < 8; j++) {
      updateSteppers(); // HACK: don't let scanHallSensors() block stepper motor operation
      int sqr = squareMap[i*8+j];
      int val = analogRead(j);
      bool occ = val > (analogThreshold[sqr] + 35);
      if (squareOccupied[sqr] != occ) {
        squareOccupied[sqr] = occ;
        lastChange[sqr] = millis();
      }
    }
  }
}

void analogScanHallSensors() {
  int maxRead[64];
  for (int i = 0; i < 64; i++)
    maxRead[i] = 0;
  for (int n = 0; n < 100; n++) {
  for (int i = 0; i < 8; i++) {
    digitalWrite(bit1pin, i&1);
    digitalWrite(bit2pin, i&2);
    digitalWrite(bit3pin, i&4);
    // XXX: do we need to wait between writing to the bit pins and reading from the analogue pins?
    for (int j = 0; j < 8; j++) {
      int sqr = squareMap[i*8+j];
      int val = analogRead(j);
      if (val > maxRead[sqr])
        maxRead[sqr] = val;
    }
  }
  delay(10);
  }

  for (int i = 0; i < 64; i++) {
    Serial.print(i); Serial.print(" = "); Serial.print(maxRead[i]); Serial.print("; ");
    if (i % 8 == 7)
      Serial.print("\n");
  }
}

// XXX: returns pointer to static buffer
char *square2Name(int square) {
  static char s[3];
  
  if (square < 0 || square > 63) {
    s[0] = 'x'; s[1] = 'x'; s[2] = 0;
    return s;
  }

  s[0] = (square/8) + 'a';
  s[1] = (square%8) + '1';
  s[2] = 0;
  return s;
}

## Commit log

2020-03-03 Add xbracket-idler
    [assembly.FCStd, linearbearing.FCStd, railbracket.FCStd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]
2020-03-03 Add xbracket-stepper
    [assembly.FCStd, woodenframe.FCStd, xbracket-idler.FCStd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]
2020-03-05 Add carriage
    [assembly.FCStd, carriage.FCStd, linearbearing.FCStd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]
2020-03-05 Add electromagnet, top part of carriage, NEMA17 stepper
    [NEMA-17_Stepper_Motor_40mm.fcstd, assembly.FCStd, carriage.FCStd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]
2020-03-06 Add ybracket-stepper
    [assembly.FCStd, linearrod.FCStd, woodenframe.FCStd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]
2020-03-06 Add ybracket-idler
    [assembly.FCStd, woodenframe.FCStd, ybracket-idler.FCStd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]
2020-03-23 Update CAD model
    [assembly.FCStd, electromagnet.FCStd, woodenframe.FCStd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]
2020-03-23 Add KiCad project
    [autopatzer-B_Cu.gbr, autopatzer-B_Mask.gbr, autopatzer-B_SilkS.gbr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]
2020-03-23 Add arduino project
2020-03-23 Track piece up/down, disable magnet if it is left on for too long
    [autopatzer.ino, hallsensors.ino, steppers.ino]
2020-03-25 Understand capture inputs from the board
2020-03-25 Simple captures when moving motors
2020-04-04 Move magnet code into separate file, set per-square hall sensor threshold, add electromagnetic homing
    The EM homing doesn't work properly so is currently disabled, and in practice I don't think it can
    work very well most of the time anyway.
    [autopatzer.ino, hallsensors.ino, magnet.ino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]
2020-04-11 Update hall sensor thresholds, improvement movementCost(), start of supporting en passant
2020-04-12 Move freecad files into freecad/
    [NEMA-17_Stepper_Motor_40mm.fcstd, assembly.FCStd, carriage.FCStd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]
2020-04-21 Add picase model
    [picase.FCStd]
2020-04-25 Rename directories
    [autopatzer-B_Cu.gbr, autopatzer-B_Mask.gbr, autopatzer-B_SilkS.gbr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]
2020-04-25 Add autopatzerd
    [picase.FCStd]
2020-04-27 Update picase
    [picase.FCStd]
2020-04-30 Things:
    Moves list autoscrolling
    Moves converted to PGN
    Timers
2020-05-02 Add Autopatzer::Button with switch debouncing
2020-05-02 Send board changes to websocket clients
2020-05-02 Check occupied on board rather than in game
2020-05-02 Monitor interrupts with Python instead of Perl
2020-05-02 Pass pin number to gpiomon instead of hardcoding
2020-05-05 Add minimum path cost to priority queue insertion
    The old version was mainly so slow because it was spending lots of time
    considering various piece displacements nearby, because they are short
    movements and come up first in the queue. Instead of ordering by the
    path length *so far*, we should order the queue by the minimum path length
    to the end state.
    I guess this is now more A* than Dijkstra?
2020-05-06 15% performance gain
    We don't need to keep track of which squares on the board are occupied by the piece
    we're trying to move, because it can never crash into itself.
2020-05-07 Stop timers if game has ended
2020-05-07 Log messages sent and received
    [picase.FCStd]
2020-05-09 Stiffen up the ybracket-idler
    [ybracket-idler.FCStd]
2020-05-09 Show current games in progress immediately, without waiting for timer to fire
2020-05-09 Add power off button (but right justify is not working)
2020-05-09 Wiggle the motors to wake the user up if he is to move at the start of the game
2020-05-10 Add unit test of Autopatzer::Input, and fix a couple of bugs
2020-05-10 setBoardChanges with the on-screen confirm button, and fix React warnings about missing dependencies
2020-05-10 Revert "setBoardChanges with the on-screen confirm button, and fix React warnings about missing dependencies"
    This reverts commit b268a58217f464a9429496941b05e9552f21380b.
2020-05-10 Set board changes when using the on-screen button
2020-05-11 Make confirm move button text bigger
2020-05-11 Add leave/resign/draw buttons
2020-05-12 Only clear board changes on button hit if there was a legal move
2020-05-12 Confirmation of poweroff
2020-05-12 Align IP address and power-off buttons
2020-05-12 Write an initial blank line to the Teensy
2020-05-12 Use flexbox to push buttons to the bottom
2020-05-13 Grid layout of BoardChanges and ConfirmMove
2020-05-13 Don't need a button if no move
2023-10-03 No PCBs
